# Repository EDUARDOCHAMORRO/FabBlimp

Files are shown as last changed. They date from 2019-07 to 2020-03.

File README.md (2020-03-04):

# [Fab Blimp] Workshop

 Workshop developped for Fab15 Egypt Conference by Eduardo Chamorro and Santi Fuentemilla

 Workshop of producing and fabricating a phone controlled blimp. Pcb fabricated with a Roland SRM20, blimp balloon produced by sealing a plastics bags with a CO2 lasercutter and frame made out of cardboard cutted also with the lasercutter.
 Control of the blimp via an smartphone accessing the ip address of the ESP12 via an internal wifi access point(wifi connection required)

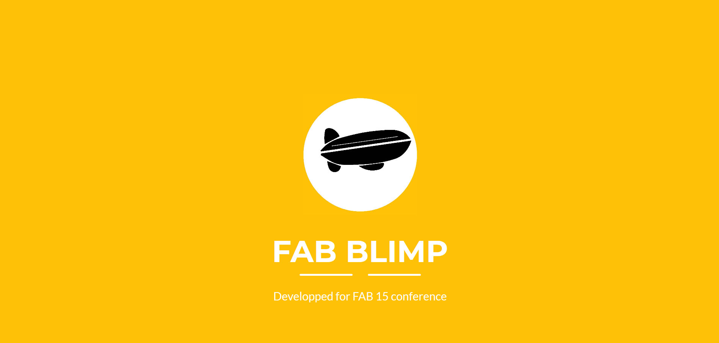
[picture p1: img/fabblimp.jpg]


[PDF DOWNLOAD GUIDE ON HOW TO ASSEMBLE IT](https://eduardochamorro.github.io/FabBlimp/fabblimp.pdf)

## Hardware Requirements

- Pcb Fr1
- 3x brushed motors 0615 size
- 3x propellers tinywhoop
- Ftdi cable 3.3v
- Corrugated Card 360 kg/m3
- Glue gun
-	Double side tape
- Cutters
-	Scissors
- Helium Kit ,Tank 14.9 cu.ft
- 36 Inch Giant Latex Balloon White
- Electronics		RES 100 OHM 1/4W 1% 1206 SMD
- Electronics		RES 10.0K OHM 1/4W 1% 1206 SMD
- Electronics		CAP CER 4.7UF 35V Y5V 1206
- Electronics		CAP CER 10UF 35V Y5V 1206
- Electronics		MOSFET N-CH 30V 1.7A SSOT3
- Electronics		SMT RT Angle Male Header 0.1" (36pos)
- Electronics		SWITCH TACT SMD W-GND 160GF
- Electronics		Esp8266 Esp-12e
- Electronics		IC REG LDO 3.3V 1A SOT223-3

## PCB production files

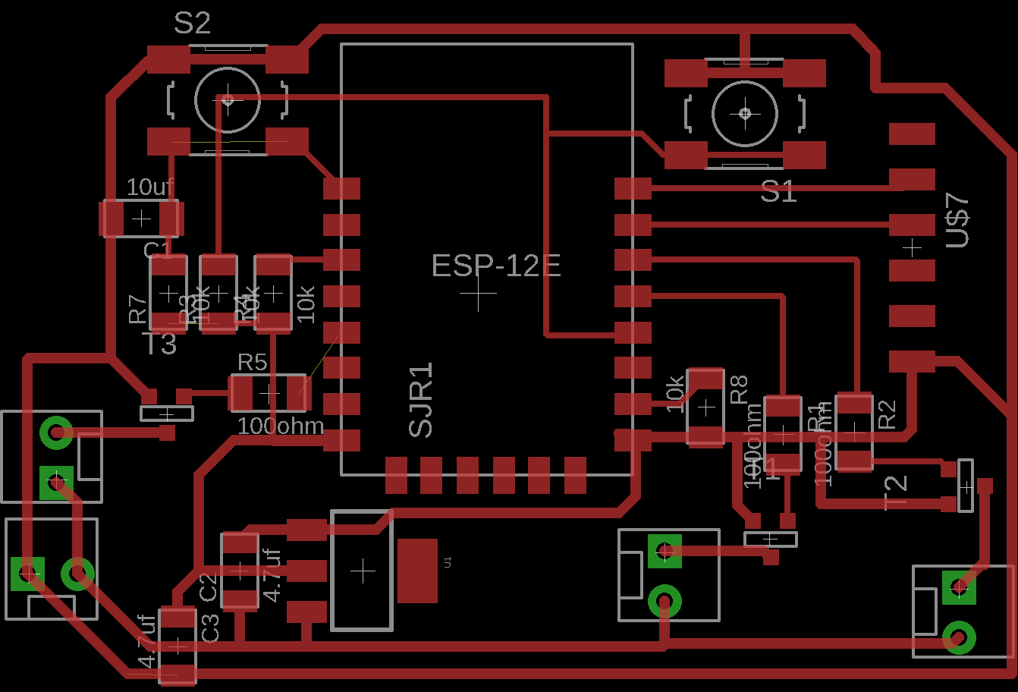
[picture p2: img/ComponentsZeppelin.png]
Electronic Components


**FILES WITH MOTOR HOLDER**
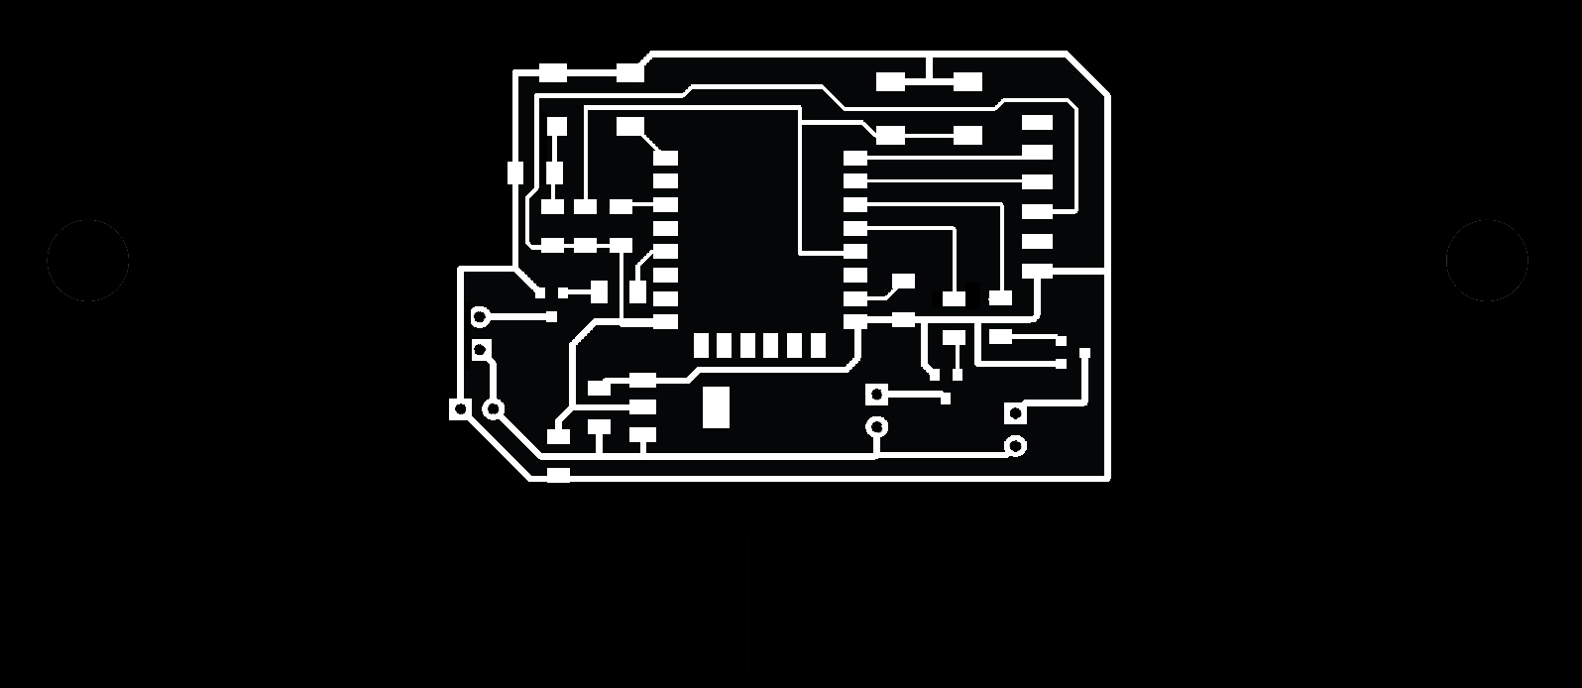
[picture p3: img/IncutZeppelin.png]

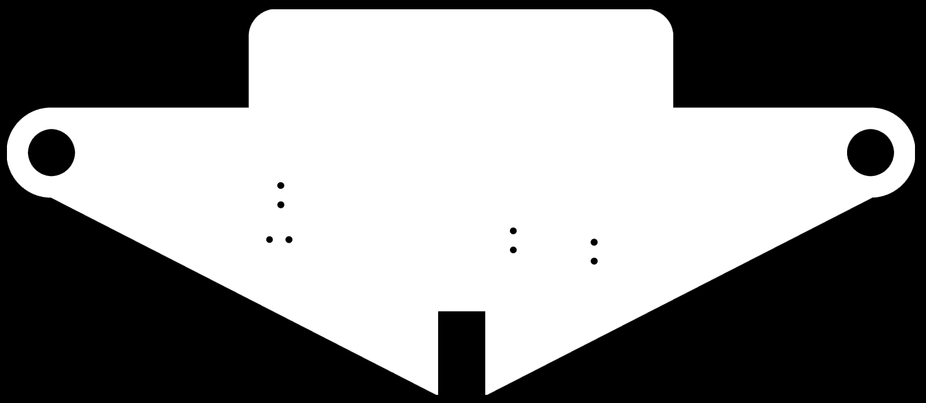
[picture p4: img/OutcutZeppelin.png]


**FILES WITHOUT MOTOR HOLDER**
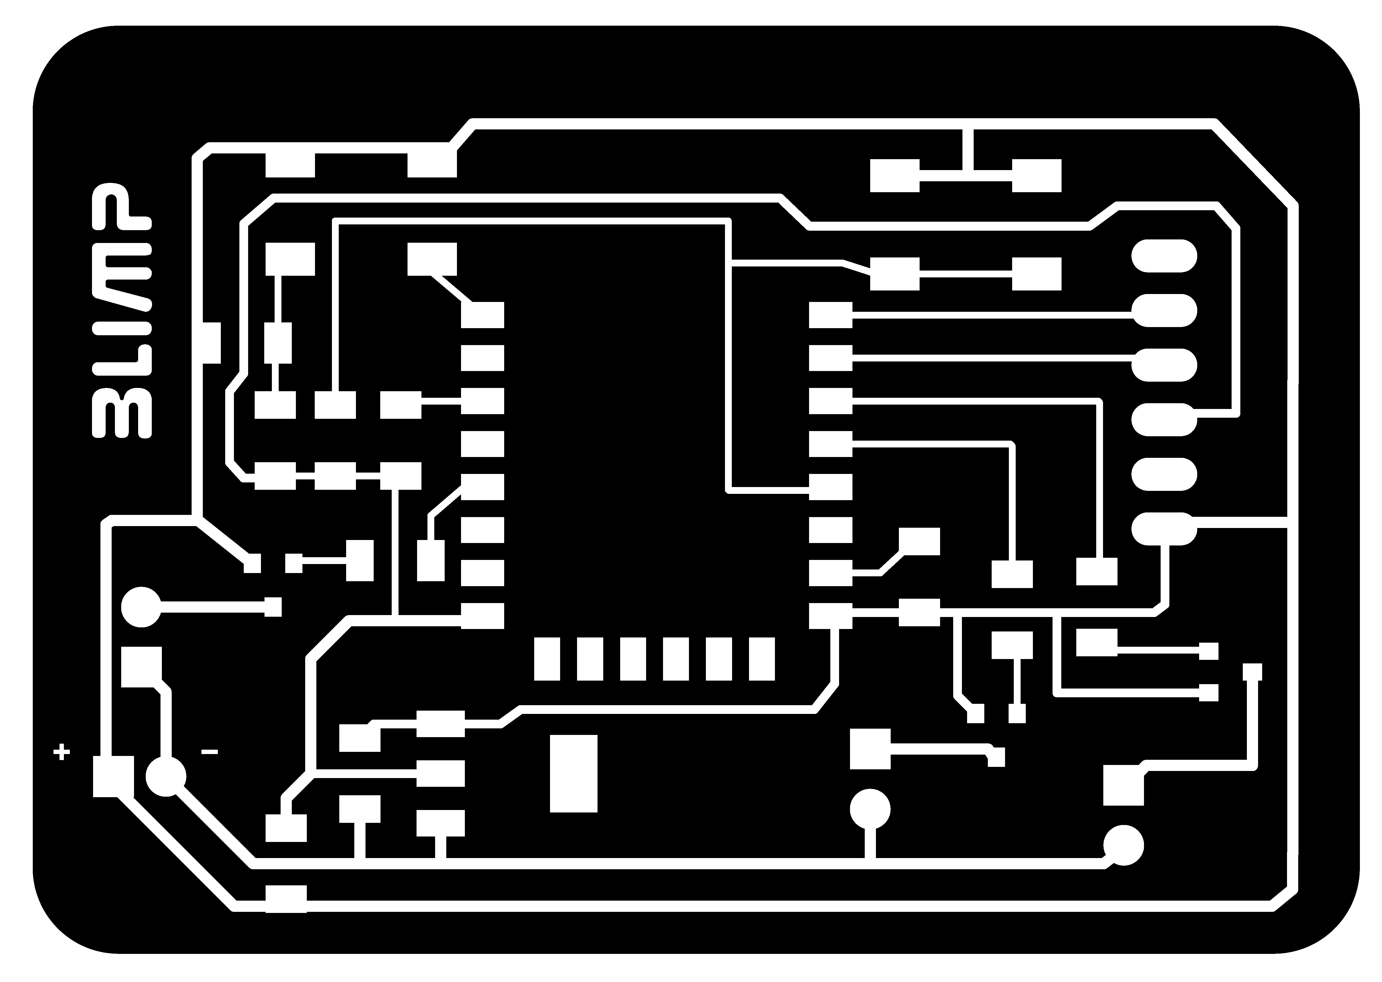
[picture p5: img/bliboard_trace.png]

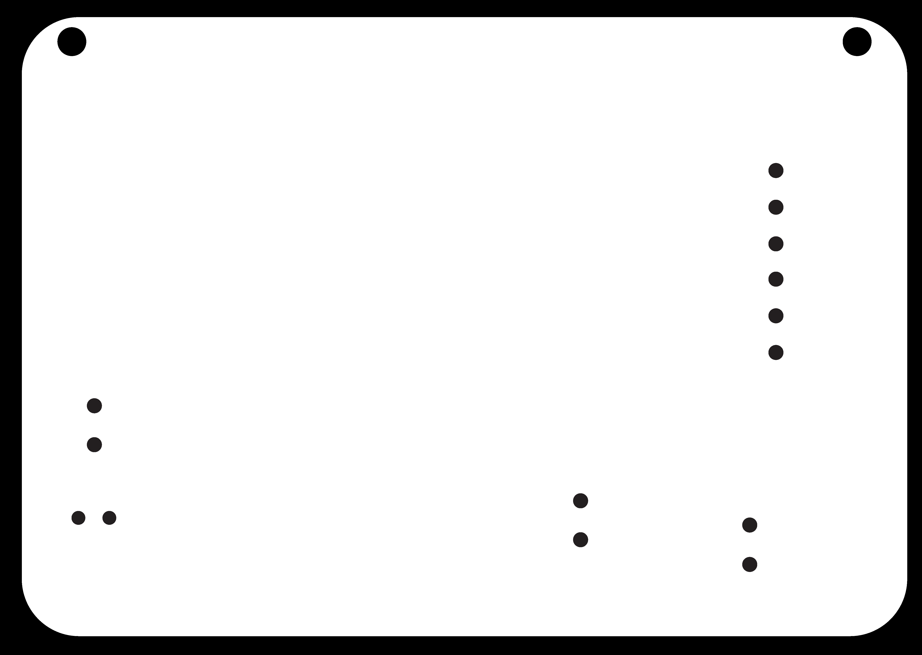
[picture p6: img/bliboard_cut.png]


## Cut out file for a lasercutter motor holder

[Download Laser Cut file dxf](https://eduardochamorro.github.io/FabBlimp/dock.dxf)

## Control app via browser

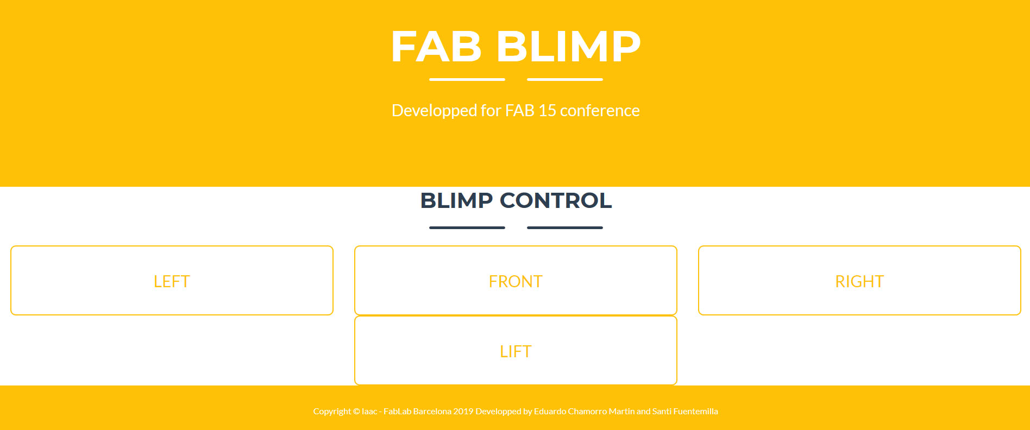
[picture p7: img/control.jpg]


There is two version of the code.

1- WIFI SERVER : the blimp connects to an already existing wifi hotspot and uses that network to increase the control range and improved webpage control.(longer range and more visual)

2- WIFI HOTSPOT : for not stable or fast enough wifi hotspots, the blimp creates his own hotspot and get controlled by publishing an control webpage.(faster control,shorter range and less visual)

## Copyright and License

Copyright3-2019 FabLab BCN - IaaC. Code released under the [MIT](https://github.com/BlackrockDigital/startbootstrap-freelancer/blob/gh-pages/LICENSE) license.
Developped by Eduardo Chamorro and Santi Fuentemilla. July 2019
Updated by Miriam Choi February 2020

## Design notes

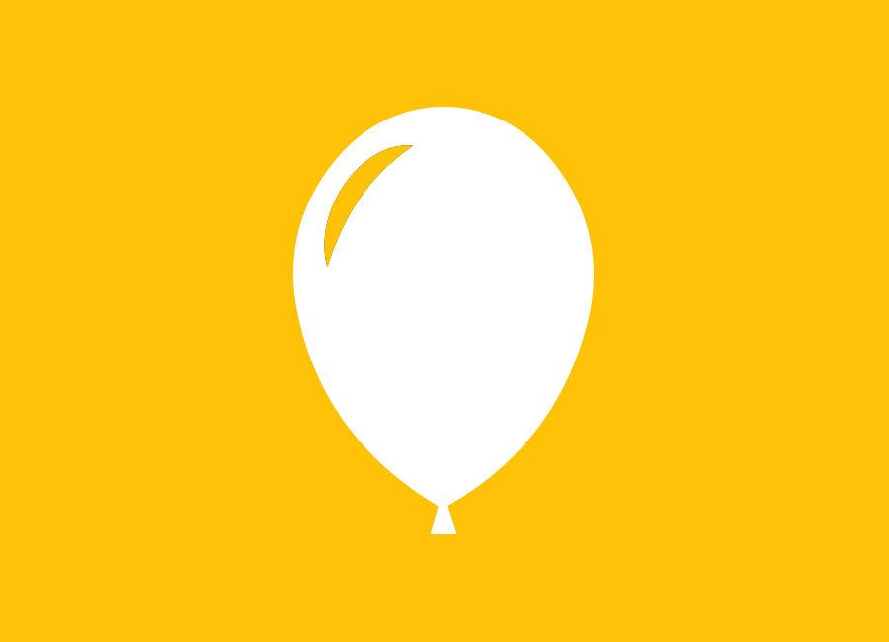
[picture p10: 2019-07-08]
webpage/img/portfolio/up.png

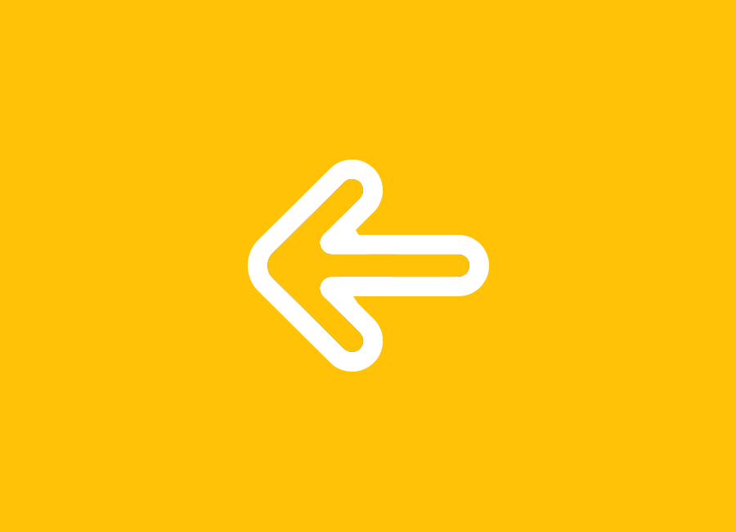
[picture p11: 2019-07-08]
webpage/img/portfolio/left.png

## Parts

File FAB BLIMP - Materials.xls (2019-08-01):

FAB BLIMP
qty | name | ID | LINK
3 | RES 100 OHM 1/4W 1% 1206 SMD | 311-100FRCT-ND | https://www.digikey.com/products/en?keywords=311-100FRCT-ND
4 | RES 10.0K OHM 1/4W 1% 1206 SMD | 311-10.0KFRCT-ND | https://www.digikey.com/products/en?keywords=311-10.0KFRCT-ND
2 | CAP CER 4.7UF 35V Y5V 1206 | 587-2254-1-ND | https://www.digikey.com/products/en?keywords=587-2254-1-ND
1 | CAP CER 10UF 35V Y5V 1206 | 587-1352-1-ND | https://www.digikey.com/products/en?keywords=587-1352-1-ND
3 | MOSFET N-CH 30V 1.7A SSOT3 | NDS355ANCT-ND | https://www.digikey.com/products/en?keywords=NDS355ANCT-ND
1 | SMT RT Angle Male Header 0.1" (36pos) | 1528-1000-ND | https://www.digikey.com/products/en?keywords=S1143E-36-ND%09
2 | SWITCH TACT SMD W-GND 160GF | SW262CT-ND | https://www.digikey.com/product-detail/en/B3SN-3112P/SW262CT-ND
1 | Esp8266 Esp-12e | Esp8266 Esp-12e | https://www.amazon.com/Esp8266-Esp-12e-Wireless-Transceiver-IFANCY-TECH/dp/B01GZ0687C
1 | IC REG LDO 3.3V 1A SOT223-3 | ZLDO1117G33DICT-ND | https://www.digikey.com/products/en?keywords=ZLDO1117G33DICT-ND%09
0.5 | Hélice Propulsor Propeller | JJRC H36 Eachine | https://www.amazon.es/Fytoo-Propulsor-Propeller-Helic%C3%B3ptero-Accesorio/dp/B077PN1TP1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
1 | 1 pack of 4, 6x15mm motor-17500KV TW |  | https://www.amazon.es/Crazepony-UK-4pcs-6x15mm-motore-velocit%C3%A0/dp/B06XNPP7RB
1 | Lipo, 250mah 30C Batería Lipo con Conector PH2.0 |  | https://www.amazon.es/Bater%C3%ADa-Conector-Happymodel-Mobula7-bater%C3%ADas/dp/B07Q1HTCR3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 (https://www.amazon.es/Batería-Conector-Happymodel-Mobula7-baterías/dp/B07Q1HTCR3?__mk_es_ES=ÅMÅŽÕÑ&rnid=831276031&s=electronics)
1 | Single side circuit board stock | PCB - 100x150 mm | https://www.inventables.com/technologies/circuit-board-blanks
1 | Solder stations
1 | corrugated Card 360 kg/m3 |  | https://www.mwmaterialsworld.com/es/plancha-de-carton-microcanal-colores-360kg-m3.html
0.5 | Glue gun |  | https://www.amazon.com/ccbetter-Upgraded-Removable-Anti-hot-Flexible/dp/B01178RVI2?s=gateway
1 | Double side tape
0.5 | Cutters
0.5 | Scissors
0.5 | Helium Kit ,Tank 14.9 cu.ft |  | https://www.amazon.com/Balloon-Time-Disposable-Helium-cu-ft/dp/B0748X9KVF?s=gateway
0.5 | 36 Inch Giant Latex Balloon White |  | https://www.amazon.com/dp/B07D9SCYD2

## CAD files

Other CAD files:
dock.dxf

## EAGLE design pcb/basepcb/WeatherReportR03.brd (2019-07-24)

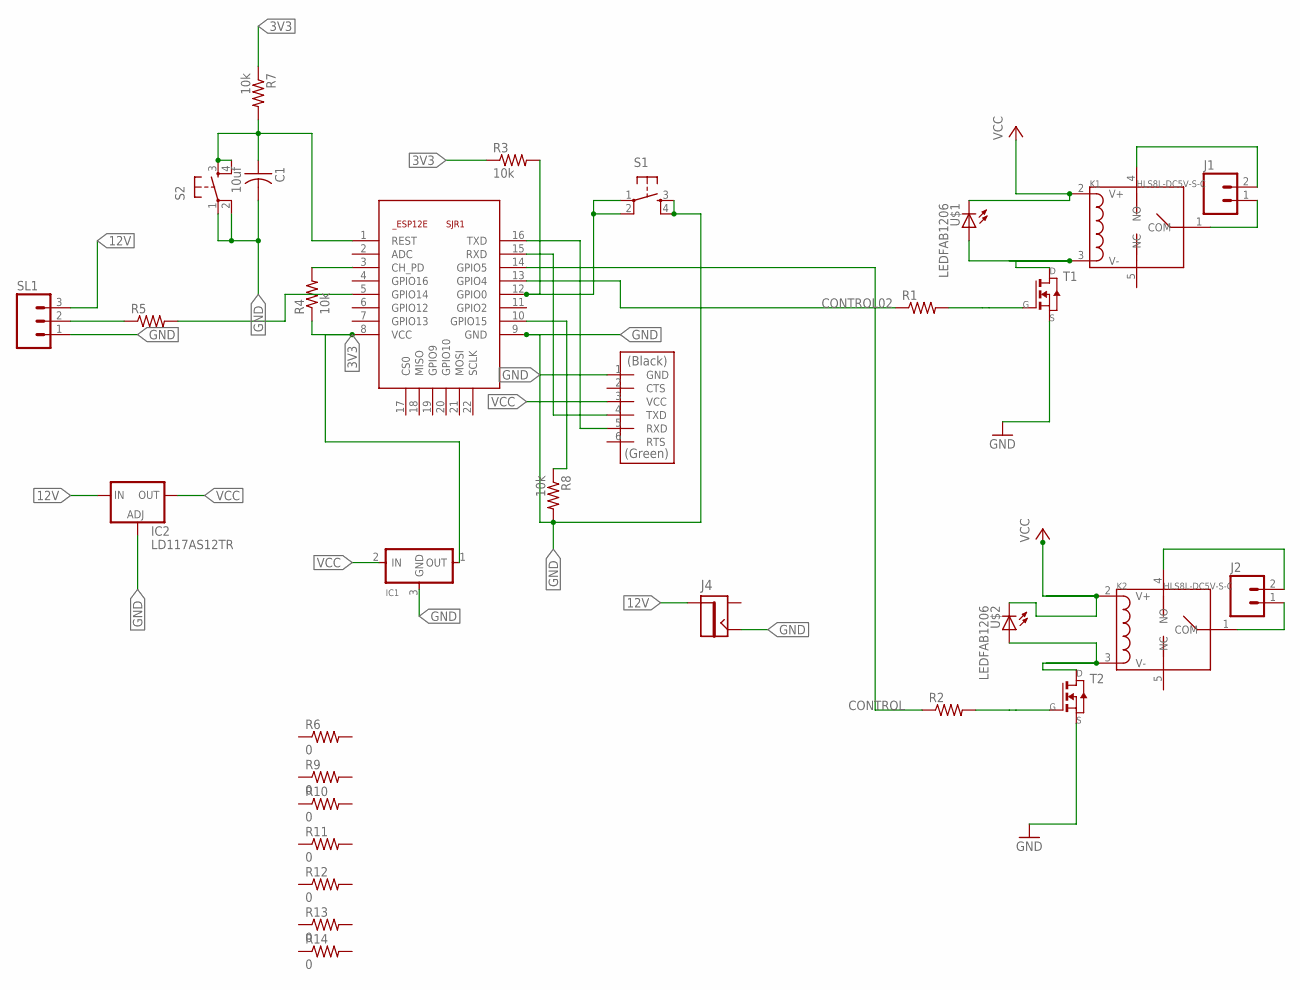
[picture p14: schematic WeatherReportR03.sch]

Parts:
C1: 10uf; C1206FAB
IC1: REGULATORSOT23; SOT23
IC2: LD117AS12TR; SOT223
J1, J2: M02POLAR_LOCK; MOLEX-1X2_LOCK
J4: JACK2.1MM; JACK_2.1MM
K1, K2: HLS8L-DC5V-S-C; REY5-19.0X15.0X15.0MM
R1, R2, R5: RES-US1206FAB; R1206FAB
R3, R4, R7, R8: 10k; R1206FAB
R6, R9, R10, R11, R12, R13, R14: 0; R1206FAB
S1, S2: 6MM_SWITCH6MM_SWITCH; 6MM_SWITCH
SJR1: ESP8266-12EESP12E; ESP8266-ESP12E
SL1: M03; 03P
T1, T2: NMOSFETSOT23; SOT-23
U$1, U$2: LEDFAB1206; LED1206FAB
U$7: FTDI-SMD-HEADER; 1X06SMD

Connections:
3V3: IC1.1 (OUT), R3.1, R4.1, R7.1, SJR1.8 (VCC)
12V: IC2.3 (IN), J4.PIN, SL1.3
CONTROL: R2.1, SJR1.14 (GPIO5)
CONTROL02: R1.1, SJR1.13 (GPIO4)
GND: C1.2, IC1.3 (GND), IC2.1 (ADJ), J4.CONTACT, R8.2, S1.3 (S), S1.4 (S1), S2.1, S2.2 (P1), SJR1.9 (GND), SL1.1, T1.2 (S), T2.2 (S), U$7.1 (GND)
unnamed: R1.2, T1.3 (G)
unnamed: K1.3 (V-), T1.1 (D), U$1.1 (A)
unnamed: SJR1.16 (TXD), U$7.5 (RXD)
unnamed: SJR1.15 (RXD), U$7.4 (TXD)
unnamed: R8.1, SJR1.10 (GPIO15)
unnamed: J1.2, K1.4 (NO)
unnamed: J1.1, K1.1 (COM)
unnamed: R3.2, S1.1, S1.2 (P1), SJR1.12 (GPIO0)
unnamed: R5.2, SJR1.5 (GPIO14)
unnamed: K2.3 (V-), T2.1 (D), U$2.1 (A)
unnamed: C1.1, R7.2, S2.3 (S), S2.4 (S1), SJR1.1 (REST)
unnamed: R2.2, T2.3 (G)
unnamed: J2.2, K2.4 (NO)
unnamed: J2.1, K2.1 (COM)
unnamed: R4.2, SJR1.3 (CH_PD)
unnamed: R5.1, SL1.2
VCC: IC1.2 (IN), IC2.4 (OUT), K1.2 (V+), K2.2 (V+), U$1.2 (C), U$2.2 (C), U$7.3 (VCC)

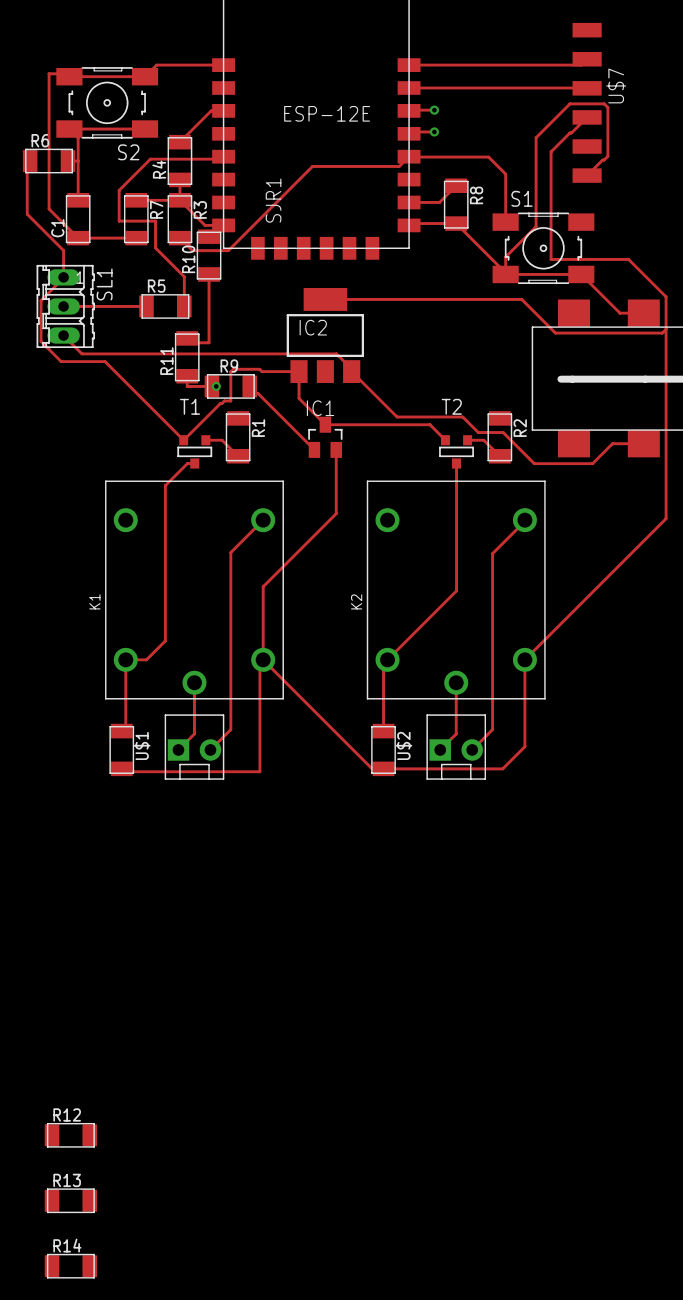
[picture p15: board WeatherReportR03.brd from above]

Board: 2 copper layers, 31 parts (0 on the bottom side), 22 nets.

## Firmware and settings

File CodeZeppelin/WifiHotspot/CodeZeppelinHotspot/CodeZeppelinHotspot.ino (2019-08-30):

/*******************************************************************
    A sketch for controlling a Small Blimp with using a web page
    hosted on a ESP12
    Code by:
    /* Eduardo Chamorro Martin - eduardochamorromartin@gmail.com - http://eduardochamorro.github.io/beansreels/index.html
    Based on the code developped by Brian Lough

 *******************************************************************/

#include <ESP8266WiFi.h>
#include <WiFiClient.h>
#include <ESP8266WebServer.h>
#include <ESP8266mDNS.h>


// These are the pins used to control the motor shield

#define MOTOR_DIRECTION2 D2 // Motor Right
#define MOTOR_DIRECTION1 D5 // Motor Left
#define MOTOR_LIFT D1 // Motor Up
#define CONNECTION D4 // Motor Up

// drivePower sets how fast the car goes
// Can be set between 0 and 1023 (although car problaly wont move if values are too low)
int LiftPower = 1023;

// steeringPower sets how fast the car turns
// Can be set between 0 and 1023 (again, car probably won't steer if the value is too low)
int TurningPower = 1023;


// ----------------
// Set your WiFi SSID and Password here
// ----------------
const char* ssid = "FABLIMPLEO";
const char* password = "12345678";



/* Put IP Address details */
IPAddress local_ip(192,168,1,1);



IPAddress gateway(192,168,1,1);
IPAddress subnet(255,255,255,0);

ESP8266WebServer server(80);

const char *webpage =
#include "index.h"
  ;

void handleRoot() {
  server.send(200, "text/html", webpage);
}



void handleNotFound() {
  String message = "File Not Found\n\n";
  message += "URI: ";
  message += server.uri();
  message += "\nMethod: ";
  message += (server.method() == HTTP_GET) ? "GET" : "POST";
  message += "\nArguments: ";
  message += server.args();
  message += "\n";
  for (uint8_t i = 0; i < server.args(); i++) {
    message += " " + server.argName(i) + ": " + server.arg(i) + "\n";
  }
  server.send(404, "text/plain", message);
}

void setup(void) {

  pinMode(MOTOR_DIRECTION2, OUTPUT);     // Initialize the LED_BUILTIN pin as an output
  pinMode(MOTOR_DIRECTION1, OUTPUT);
  pinMode(MOTOR_LIFT, OUTPUT);
  pinMode(CONNECTION, OUTPUT);




  Serial.begin(115200);
  
  WiFi.softAP(ssid, password);
  WiFi.softAPConfig(local_ip, gateway, subnet);
  delay(100);
  

  server.on("/", handleRoot);
  
  server.begin();
  Serial.println("HTTP server started");




  server.on("/up", []() {
    Serial.println("up");
    analogWrite(MOTOR_LIFT, LiftPower);
    server.send(200, "text/plain", "up");
  });

  server.on("/driveStop", []() {
    Serial.println("driveStop");
    analogWrite(MOTOR_LIFT, 0);
    server.send(200, "text/plain", "driveStop");
  });
  server.on("/back", []() {
    Serial.println("back");
    analogWrite(MOTOR_DIRECTION1, TurningPower);
    analogWrite(MOTOR_DIRECTION2, TurningPower);
    server.send(200, "text/plain", "back");
  });

  server.on("/right", []() {
    Serial.println("right");
    analogWrite(MOTOR_DIRECTION1, TurningPower);
    server.send(200, "text/plain", "right");
  });

  server.on("/left", []() {
    Serial.println("left");
    analogWrite(MOTOR_DIRECTION2, TurningPower);
    server.send(200, "text/plain", "left");
  });

  server.on("/steerStop", []() {
    Serial.println("steerStop");
    analogWrite(MOTOR_DIRECTION2, 0);
    analogWrite(MOTOR_DIRECTION1, 0);
    server.send(200, "text/plain", "steerStop");
  });

  server.onNotFound(handleNotFound);

  server.begin();
  Serial.println("HTTP Server Started");
}

void loop(void) {
  server.handleClient();
}

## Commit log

2019-07-24 public push
    [WeatherReportR03.brd, WeatherReportR03.sch, Zeppelin.brd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]
2019-08-01 workshop push
    [FAB BLIMP - Materials.xls]
2020-03-04 update by miriam
    [dock.dxf]

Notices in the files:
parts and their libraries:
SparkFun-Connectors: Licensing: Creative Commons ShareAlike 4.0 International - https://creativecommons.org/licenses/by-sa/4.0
